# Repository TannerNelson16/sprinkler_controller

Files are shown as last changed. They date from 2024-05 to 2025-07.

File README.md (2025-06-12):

Introduction:
-
Smart irrigation controllers are overpriced and lack customizability so I set out to develop a simple and easy to use solution that is also robust and reliable. The intellidwell sprinkler controller uses custom micropython firmware developed for the ESP32. A localized server that runs right on the microcontroller allows for scheduling, smart phone control, and integration with smart home systems via MQTT. Solid state relays provide extrememely reliable switching of 24VAC solenoid sprinkler valves. A custom 24VAC to 5VDC (variable via a potentiometer) converter allows the logic to be powered from the same source as the sprinkler valve power.

Components used:
-
- ESP32 dev board - https://www.amazon.com/gp/product/B0C7C2HQ7P/ref=ppx_yo_dt_b_search_asin_title?ie=UTF8&psc=1
- Custom PCB - https://github.com/TannerNelson16/sprinkler_controller/blob/master/PCB_files/Sprinkler_Controller_V2/Sprinkler_Controller_V2/Sprinkler_Controller_V2.zip
- PCB parts - https://www.digikey.com/en/mylists/list/P86LUORYGY
- 3d printed container - https://github.com/TannerNelson16/sprinkler_controller/tree/master/V2_Enclosure
- 24v transformer - https://a.co/d/7ivDpOn
- Hardware:
  - https://a.co/d/18vTyet
  - https://a.co/d/1JvqW7l

Web UI:
-
<p float="left">
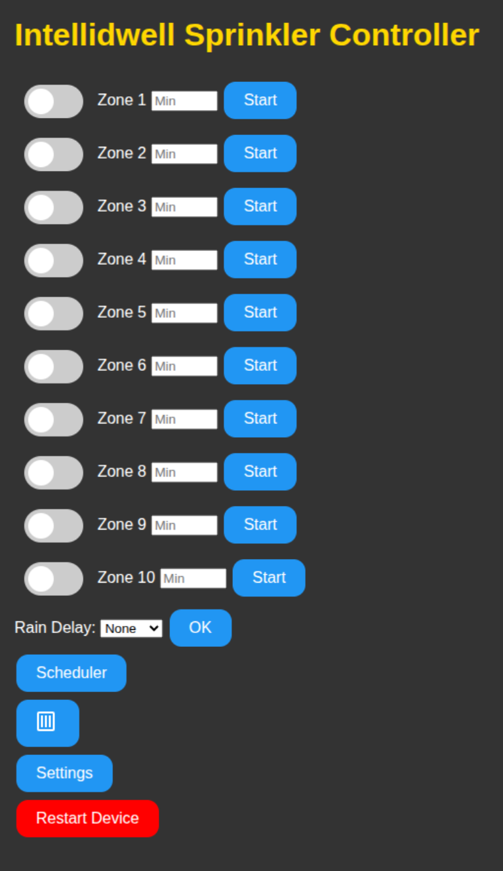
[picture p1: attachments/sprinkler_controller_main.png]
   
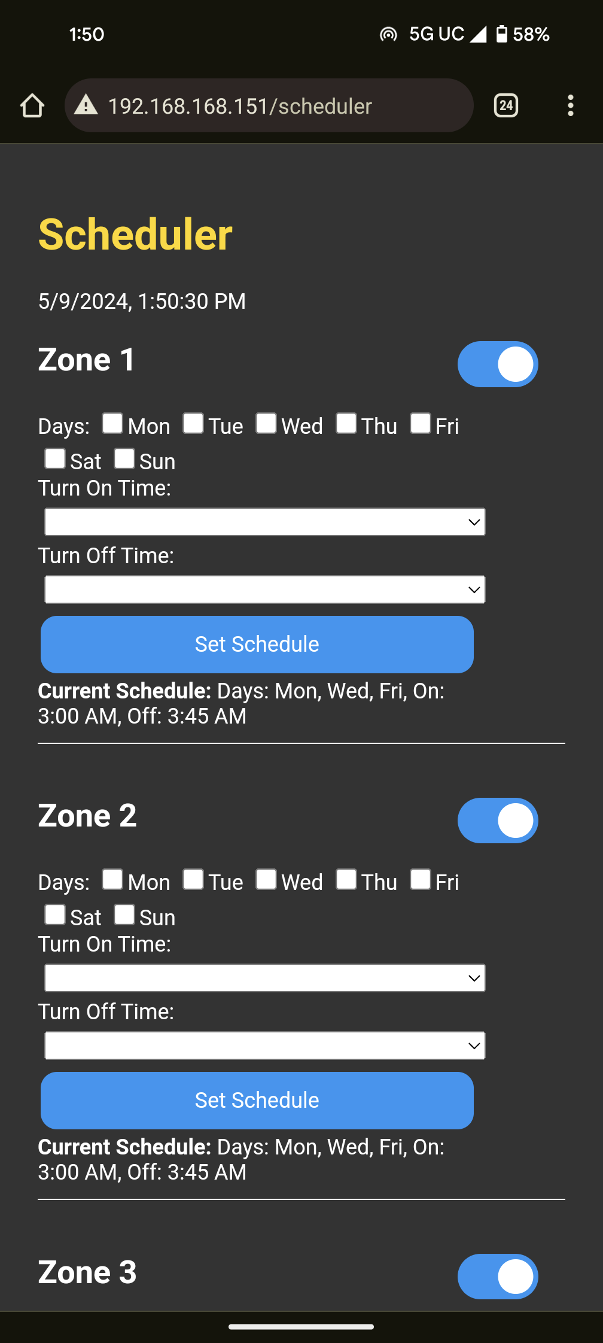
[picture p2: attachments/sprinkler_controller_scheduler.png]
  
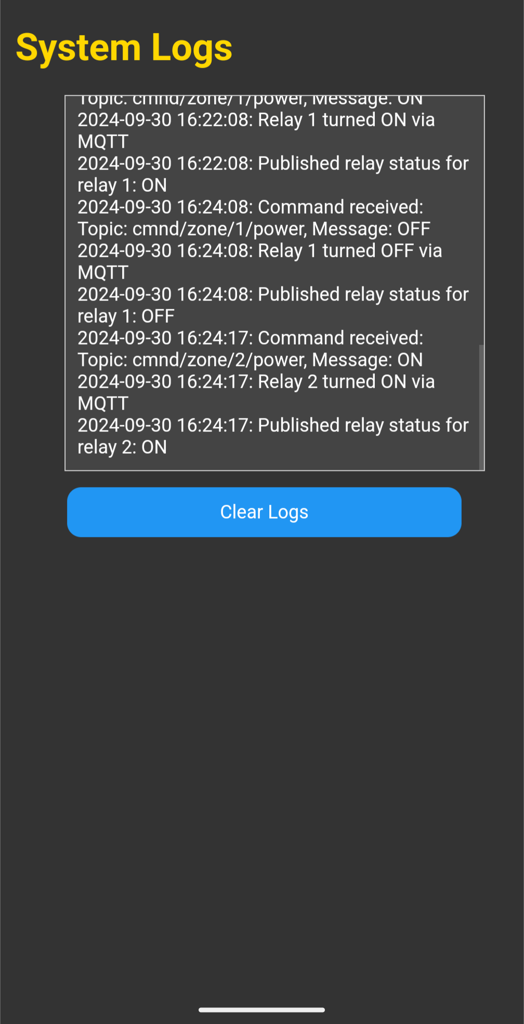
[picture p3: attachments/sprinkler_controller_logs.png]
   
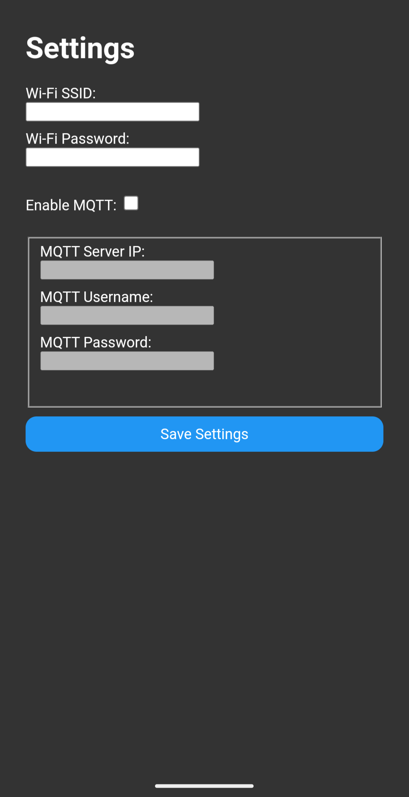
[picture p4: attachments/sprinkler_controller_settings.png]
   

</p>

Installation:
-
FOR LINUX:
--
First install the micropython environment on your ESP32. Here's the official documentation: https://docs.micropython.org/en/latest/esp32/tutorial/intro.html 

For the condensed version:
- Download micropython here: https://micropython.org/resources/firmware/ESP32_GENERIC-20240222-v1.22.2.bin
- Run the following command in the ubuntu terminal:
```
pip install esptool
```
- From the folder where the micropython file is located, run the following commands:
```
esptool.py --chip esp32 --port /dev/ttyUSB0 erase_flash
esptool.py --chip esp32 --port /dev/ttyUSB0 --baud 460800 write_flash -z 0x1000 ESP32_GENERIC-20240222-v1.22.2.bin
```
Once micropython has been successfully installed on the board, download the files in the repository navigate to it's folder.

Once this is complete, save the file and run the following commands:
```
pip install adafruit-ampy
ampy --port /dev/ttyUSB0 put index.html
ampy --port /dev/ttyUSB0 put scheduler.html
ampy --port /dev/ttyUSB0 put logs.html
ampy --port /dev/ttyUSB0 put settings.html
ampy --port /dev/ttyUSB0  put microdot.py
ampy --port /dev/ttyUSB0  put microdot_asyncio.py
ampy --port /dev/ttyUSB0  put controller.py /main.py
```
Reboot and connect to the "intellidwellSC" SSID with password "Sprinkler12345" from any device. In a browser type in 192.168.4.1 to access the sprinkler controller UI.

To connect to a Wifi Network navigate to "Settings" on the main page and enter in your WiFi credentials. You can also input your MQTT credentials here if you wish. When the device is rebooted, you can access the UI from the hostname http://sprinklers.local on your network, the IP address of the device, or from your homeassitant instance via the MQTT integration.

NOTE: If the network is unavailable, the ESP32 will first try to connect without the MQTT integration. If the network is still causing errors, the ESP32 will resume AP mode to allow for control of the sprinkler system. 

Enclosure:
-
<p float="left">
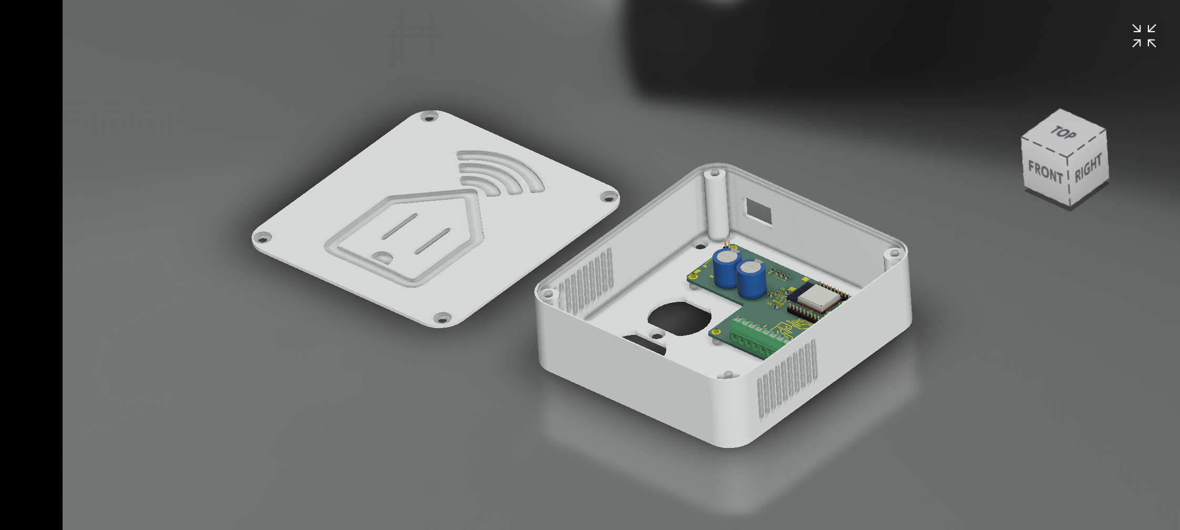
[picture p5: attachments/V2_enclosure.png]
   

Assembly:
-
PCB:
- The PCB has been tested and is fully functional.
- Download the zipped folder here: https://github.com/TannerNelson16/sprinkler_controller/blob/master/PCB_files/Sprinkler_Controller_V2/Sprinkler_Controller_V2/Sprinkler_Controller_V2.zip
- Upload the folder to jlcpcb.com or your chosen pcb manufacturer
- Purchase items from digikey to populate board: https://www.digikey.com/en/mylists/list/P86LUORYGY
- Rocker switches on amazon, if out of stock at digikey: https://a.co/d/f25Jjgr
- Once assembled, and before installing the ESP32, adjust the potentiometer to ensure a 5VDC input to vin and gnd of the ESP32.
<p float="left">
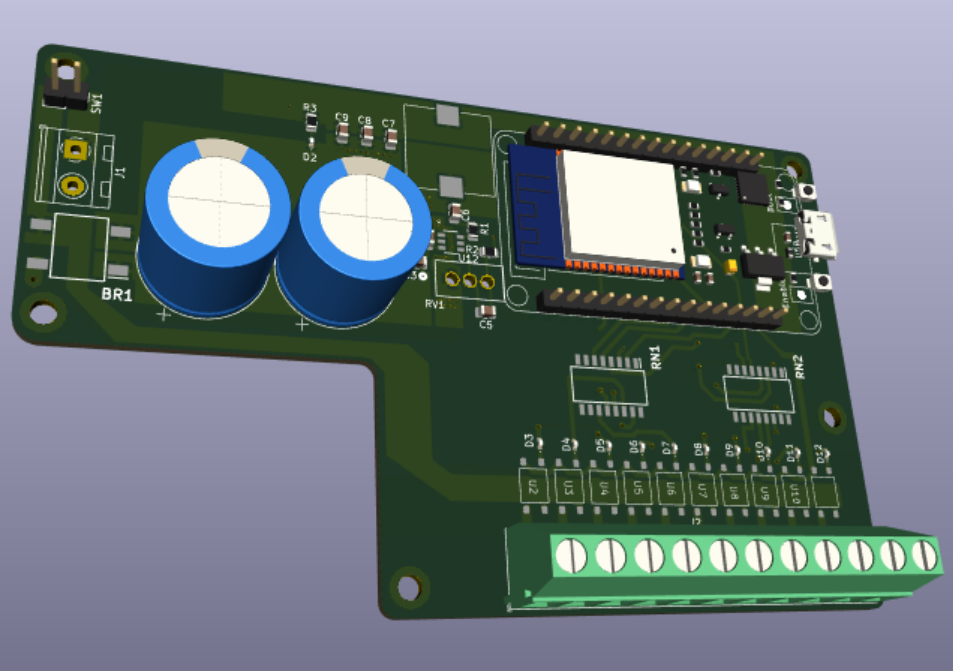
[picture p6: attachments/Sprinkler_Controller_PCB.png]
  
Final Product Images:
-
<p float="left">
   
<p float="left">
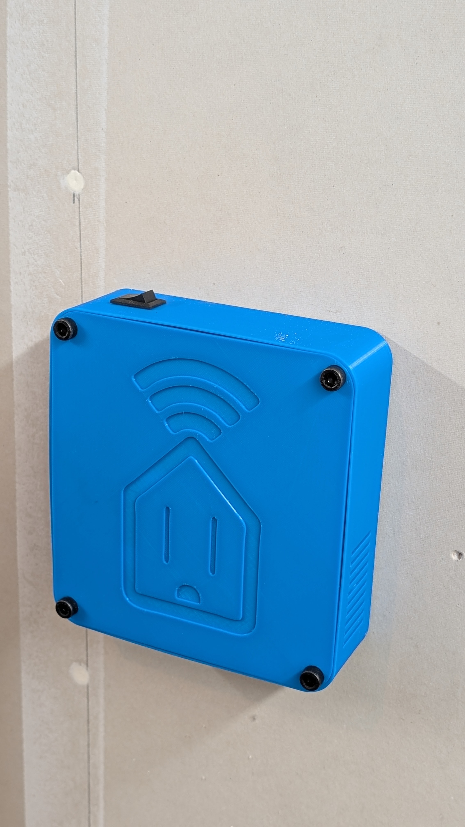
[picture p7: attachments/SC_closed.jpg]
   

Support This Project
-

If you like this project, consider supporting it with a donation!



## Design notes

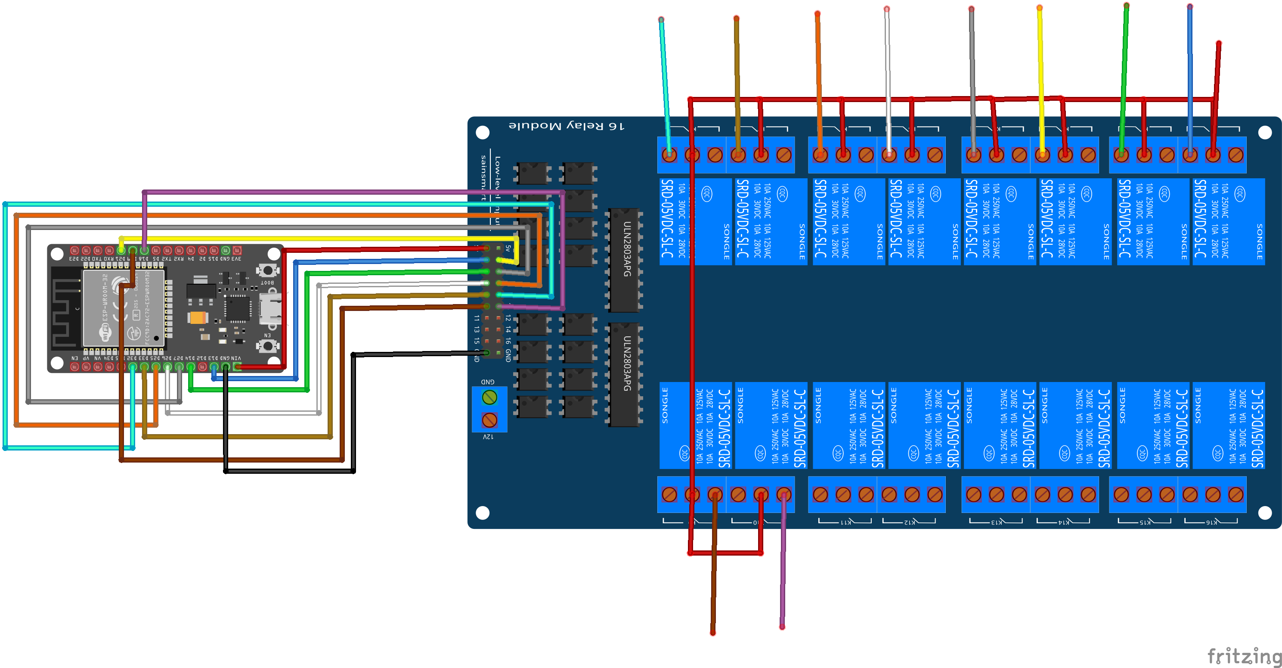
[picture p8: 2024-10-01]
attachments/pinout.png

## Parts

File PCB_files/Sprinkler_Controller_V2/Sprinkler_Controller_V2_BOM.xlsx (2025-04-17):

Country of Origin may be different at time of shipment.
The HTSUS and ECCN information shown is for informational purposes only and is not a representation or warranty as to the accuracy or reliability of these classifications. All information is provided "as is" and is subject to change without notice. Any use made of the information provided is without recourse to Digi-Key and at the user's risk.
Index | Manufacturer Part Number | Manufacturer Name | Description | Availability | Stock Status | Attrition % | Requested Quantity 1 | Pack Quantity 1 | Pack Type 1 | Digi-Key Part Number 1 | Unit Price 1 | Extended Price 1 | Minimum Order Quantity 1 | Customer Reference | Requested Part Number | Lead Weeks | Datasheet | Reference Designator | US Import Tariff | Note | Part Status | RoHS Status | Moisture Sensitivity Level (MSL) | ECCN | HTSUS | Country of Origin | Environmental Information | Original Part numbers | REACH Status | Unit of Measure | Image | Product Notes
1 | B1701URO-20D000114U1930 | Harvatek Corporation | LED RED DIFFUSED 0805 SMD | 9,763 | In Stock |  | 1 | 1 | Cut Tape (CT) | 3147-B1701URO-20D000114U1930CT-ND | 0.10000 | $0.10 | 1 |  | 3147-B1701URO-20D000114U1930TR-ND | 8 | https://mm.digikey.com/Volume0/opasdata/d220001/medias/docus/3739/B1701URO-20D000114U1930.pdf |  | N/A |  | Active | ROHS3 Compliant | 2A (4 Weeks) | EAR99 | 8541.41.0000 | Taiwan | https://mm.digikey.com/Volume0/opasdata/d220001/medias/docus/6223/Harvatek%20Corp%20REACH%20235%20Jun%202023%20Statement.pdf | 3147-B1701URO-20D000114U1930TR-ND | REACH Unaffected | EACH | https://mm.digikey.com/Volume0/opasdata/d220001/medias/images/4847/MFG_3147_B1701.jpg | Non Cancellable Non Returnable.
2 | B1701UYG-20D000114U1930 | Harvatek Corporation | LED YLW-GRN DIFFUSED 0805 SMD | 71,259 | In Stock |  | 10 | 10 | Cut Tape (CT) | 3147-B1701UYG-20D000114U1930CT-ND | 0.09900 | $0.99 | 1 |  | 3147-B1701UYG-20D000114U1930TR-ND | 8 | https://mm.digikey.com/Volume0/opasdata/d220001/medias/docus/3840/B1701UYG-20D000114U1930.pdf |  | N/A |  | Active | ROHS3 Compliant | 2A (4 Weeks) | EAR99 | 8541.41.0000 | Taiwan | https://mm.digikey.com/Volume0/opasdata/d220001/medias/docus/6223/Harvatek%20Corp%20REACH%20235%20Jun%202023%20Statement.pdf | 3147-B1701UYG-20D000114U1930TR-ND | REACH Unaffected | EACH | https://mm.digikey.com/Volume0/opasdata/d220001/medias/images/4847/MFG_3147_B1701.jpg | Non Cancellable Non Returnable.
3 | OR-M406A-TP-G | Shenzhen Orient Components Co., Ltd | SOLID STATE SPST-NO (1 FORM A) S | 2,543 | In Stock |  | 10 | 10 | Cut Tape (CT) | 5007-OR-M406A-TP-GCT-ND | 0.73500 | $7.35 | 1 |  | 5007-OR-M406A-TP-GCT-ND | 8 |  |  | N/A |  | Active | ROHS3 Compliant | 1 (Unlimited) | EAR99 | 8536.41.0030 | China |  | 5007-OR-M406A-TP-GCT-ND | REACH Unaffected | EACH
4 | DF04S | Diodes Incorporated | BRIDGE RECT 1PHASE 400V 1A DF-S | 389 | In Stock |  | 1 | 1 | Tube | DF04SDI-ND | 0.72000 | $0.72 | 1 |  | DF04SDI-ND | 12 | https://www.diodes.com/assets/Datasheets/ds17001.pdf |  | May apply on shipments to the U.S. |  | Active | ROHS3 Compliant | 1 (Unlimited) | EAR99 | 8541.10.0080 | China | https://mm.digikey.com/Volume0/opasdata/d220001/medias/docus/6731/Diode%20RoHS3%20REACH%20247%20Jan%202025%20Statement.pdf | DF04SDI-ND | REACH Unaffected | EACH | https://mm.digikey.com/Volume0/opasdata/d220001/medias/images/5773/31%7EDF-S%7E%7E4.jpg
5 | TB003-500-P02BE | Same Sky (Formerly CUI Devices) | TERMINAL BLOCK, SCREW TYPE, 5.00 | 25,783 | In Stock |  | 1 | 1 | Bag | 102-6161-ND | 0.43000 | $0.43 | 1 |  | 102-6161-ND | 18 | https://www.cuidevices.com/product/resource/tb003-500.pdf |  | May apply on shipments to the U.S. |  | Active | ROHS3 Compliant | Not Applicable | EAR99 | 8536.90.4000 | China | https://www.cuidevices.com/product/resource/material-compliance/tb003-500-series|https://www.cuidevices.com/product/resource/ce-declaration/tb003-500-series | 102-6161-ND | REACH Unaffected | EACH | https://mm.digikey.com/Volume0/opasdata/d220001/medias/images/568/MFG_TB003-500-P02BE.jpg
6 | TB001-500-11BE | Same Sky (Formerly CUI Devices) | TERMINAL BLOCK, SCREW TYPE, 5.00 | 64 | In Stock |  | 1 | 1 | Box | 102-6143-ND | 1.75000 | $1.75 | 1 |  | 102-6143-ND | 18 | https://www.cuidevices.com/product/resource/tb001-500.pdf |  | May apply on shipments to the U.S. |  | Active | ROHS3 Compliant | Not Applicable | EAR99 | 8536.90.4000 | China | https://www.cuidevices.com/product/resource/material-compliance/tb001-500-series|https://www.cuidevices.com/product/resource/ce-declaration/tb001-500-series | 102-6143-ND | REACH Unaffected | EACH | https://mm.digikey.com/Volume0/opasdata/d220001/medias/images/695/MFG_TB001-500-11BE.jpg
7 | 4816P-T01-681LF | Bourns Inc. | RES ARRAY 8 RES 680 OHM 16SOIC | 1,904 | In Stock |  | 2 | 2 | Tube | 4816P-T01-681LF-ND | 2.17000 | $4.34 | 1 |  | 4816P-T01-681LF-ND | 7 | https://www.bourns.com/docs/Product-Datasheets/4800P.pdf |  | N/A |  | Active | ROHS3 Compliant | 1 (Unlimited) | EAR99 | 8533.21.0010 | Costa Rica | https://www.bourns.com/docs/rohs-cofc/41xx_43xx_44xx_48xx_coc.pdf?sfvrsn=376d7ef6_4|https://mm.digikey.com/Volume0/opasdata/d220001/medias/docus/6657/Bourns%20REACH%20247%20Jan%202025%20Statement.pdf | 4816P-T01-681LF-ND | REACH Affected | EACH | https://mm.digikey.com/Volume0/opasdata/d220001/medias/images/6285/118%7E16SOIC-5.59%7E%7E16.jpg
8 | TPP362081-T6TR | 3PEAK | IC REG BUCK ADJ 2A TSOT23-6 | 5,990 | In Stock |  | 1 | 1 | Cut Tape (CT) | 5503-TPP362081-T6TRCT-ND | 0.47000 | $0.47 | 1 |  | 5503-TPP362081-T6TRCT-ND | 9 | https://static.3peak.com/res/doc/ds/Datasheet_TPP36208.pdf |  | May apply on shipments to the U.S. |  | Active | ROHS3 Compliant | 3 (168 Hours) | EAR99 | 8542.39.0060 | China |  | 5503-TPP362081-T6TRCT-ND | REACH Unaffected | EACH | https://mm.digikey.com/Volume0/opasdata/d220001/derivates/6/002/203/016/5503%7ETSOT23-6%7E%7E6_web%28640x640%29.jpg
9 | IFDC5050HZER150M | Vishay Dale | FIXED IND 15UH 7.1A 27 MOHM SMD | 473 | In Stock |  | 1 | 1 | Cut Tape (CT) | 541-IFDC5050HZER150MCT-ND | 0.88000 | $0.88 | 1 |  | 541-IFDC5050HZER150MCT-ND | 14 | https://www.vishay.com/doc?34612 |  | N/A |  | Active | ROHS3 Compliant | 1 (Unlimited) | EAR99 | 8504.50.8000 | Taiwan |  | 541-IFDC5050HZER150MCT-ND | REACH Unaffected | EACH | https://mm.digikey.com/Volume0/opasdata/d220001/medias/images/6128/MFG_IHLP5050FDERxxxxxx_view2.jpg | Non Cancellable Non Returnable.
10 | GRM21BR61H106KE43L | Murata Electronics | CAP CER 10UF 50V X5R 0805 | 158,384 | In Stock |  | 1 | 1 | Cut Tape (CT) | 490-18663-1-ND | 0.28000 | $0.28 | 1 |  | 490-18663-1-ND | 10 | https://search.murata.co.jp/Ceramy/image/img/A01X/G101/ENG/GRM21BR61H106KE43-01A.pdf |  | N/A |  | Active | ROHS3 Compliant | 1 (Unlimited) | EAR99 | 8532.24.0020 | Japan |  | 490-18663-1-ND | REACH Unaffected | EACH | https://mm.digikey.com/Volume0/opasdata/d220001/medias/images/5447/490-Ceramic-Capacitor-Tan-Field.jpg
11 | C2012X5R1V226M125AC | TDK Corporation | CAP CER 22UF 35V X5R 0805 | 137,454 | In Stock |  | 2 | 2 | Cut Tape (CT) | 445-14428-1-ND | 0.58000 | $1.16 | 1 |  | 445-14428-1-ND | 24 | https://product.tdk.com/system/files/dam/doc/product/capacitor/ceramic/mlcc/catalog/mlcc_commercial_general_en.pdf |  | N/A |  | Active | ROHS3 Compliant | 1 (Unlimited) | EAR99 | 8532.24.0020 | Japan | https://product.tdk.com/system/files/dam/doc/product/capacitor/ceramic/mlcc/rohs/mlccrohs_commercial_general_en.pdf|https://product.tdk.com/en/environment/index.html | 445-14428-1-ND | REACH Unaffected | EACH | https://mm.digikey.com/Volume0/opasdata/d220001/medias/images/4846/445_0805-%282012-Metric%29-1%2C45mm-C-Series.jpg
12 | RC0805JR-070RL | YAGEO | RES 0 OHM JUMPER 1/8W 0805 | 269,822 | In Stock |  | 1 | 1 | Cut Tape (CT) | 311-0.0ARCT-ND | 0.10000 | $0.10 | 1 |  | 311-0.0ARCT-ND | 18 | https://www.yageo.com/upload/media/product/products/datasheet/rchip/PYu-RC_Group_51_RoHS_L_12.pdf |  | N/A |  | Active | ROHS3 Compliant | 1 (Unlimited) | EAR99 | 8533.21.0030 | Taiwan | https://www.yageo.com/en/Download/Index/certificates#rchip | 311-0.0ARCT-ND | REACH Unaffected | EACH | https://mm.digikey.com/Volume0/opasdata/d220001/medias/images/4322/cut-tape-render.jpg
13 | CC0805KRX7R9BB104 | YAGEO | CAP CER 0.1UF 50V X7R 0805 | 2,885,384 | In Stock |  | 1 | 1 | Cut Tape (CT) | 311-1140-1-ND | 0.08000 | $0.08 | 1 |  | 311-1140-1-ND | 16 | https://www.yageo.com/upload/media/product/productsearch/datasheet/mlcc/UPY-GPHC_X7R_6.3V-to-250V_24.pdf |  | N/A |  | Active | ROHS3 Compliant | 1 (Unlimited) | EAR99 | 8532.24.0020 | Taiwan |  | 311-1140-1-ND | REACH Unaffected | EACH | https://mm.digikey.com/Volume0/opasdata/d220001/medias/images/4322/cut-tape-render.jpg
14 | RMCF0805FT49R9 | Stackpole Electronics Inc | RES 49.9 OHM 1% 1/8W 0805 | 165,093 | In Stock |  | 1 | 1 | Cut Tape (CT) | RMCF0805FT49R9CT-ND | 0.10000 | $0.10 | 1 |  | RMCF0805FT49R9CT-ND | 17 | https://www.seielect.com/catalog/sei-rmcf_rmcp.pdf |  | N/A |  | Active | ROHS3 Compliant | 1 (Unlimited) | EAR99 | 8533.21.0030 | Taiwan | https://www.seielect.com/catalog/SEI-RoHS_Compliance_Status.pdf|https://www.seielect.com/catalog/reach.pdf|https://www.seielect.com/catalog/sei-coc%20prop%2065.pdf | RMCF0805FT49R9CT-ND | REACH Unaffected | EACH | https://mm.digikey.com/Volume0/opasdata/d220001/medias/images/639/0805-RMCF-Series.jpg
15 | 3296W-1-253LF | Bourns Inc. | TRIMMER 25K OHM 0.5W PC PIN TOP | 988 | In Stock |  | 1 | 1 | Tube | 3296W-253LF-ND | 2.05000 | $2.05 | 1 |  | 3296W-253LF-ND | 10 | https://www.bourns.com/docs/product-datasheets/3296.pdf |  | N/A |  | Active | ROHS3 Compliant | Not Applicable | EAR99 | 8533.40.8050 | Costa Rica | https://www.bourns.com/docs/rohs-cofc/cofc_trim1.pdf?sfvrsn=ec972807_4|https://mm.digikey.com/Volume0/opasdata/d220001/medias/docus/6657/Bourns%20REACH%20247%20Jan%202025%20Statement.pdf | 3296W-253LF-ND | REACH Unaffected | EACH | https://mm.digikey.com/Volume0/opasdata/d220001/medias/images/2383/3296W%20SERIES.jpg
16 | UVK1H102MHD | Nichicon | CAP ALUM 1000UF 20% 50V RADIAL | 532 | In Stock |  | 2 | 2 | Bulk | 493-16111-ND | 1.19000 | $2.38 | 1 |  | 493-16111-ND | 20 | https://www.nichicon.co.jp/english/series_items/catalog_pdf/e-uvk.pdf |  | N/A |  | Active | ROHS3 Compliant | Not Applicable | EAR99 | 8532.22.0020 | Malaysia |  | 493-16111-ND | REACH Affected | EACH | https://mm.digikey.com/Volume0/opasdata/d220001/medias/images/2583/VK%20SERIES%2027mm.JPG
17 | RNCP0805FTD1K00 | Stackpole Electronics Inc | RES 1K OHM 1% 1/4W 0805 | 256,179 | In Stock |  | 1 | 1 | Cut Tape (CT) | RNCP0805FTD1K00CT-ND | 0.10000 | $0.10 | 1 |  | RNCP0805FTD1K00TR-ND | 17 | https://www.seielect.com/catalog/sei-rncp.pdf |  | N/A |  | Active | ROHS3 Compliant | 1 (Unlimited) | EAR99 | 8533.21.0030 | Taiwan | https://www.seielect.com/catalog/SEI-RoHS_Compliance_Status.pdf|https://www.seielect.com/catalog/reach.pdf|https://www.seielect.com/catalog/sei-coc%20prop%2065.pdf | RNCP0805FTD1K00TR-ND | REACH Unaffected | EACH | https://mm.digikey.com/Volume0/opasdata/d220001/medias/images/4322/cut-tape-render.jpg
18 | PPTC151LFBN-RC | Sullins Connector Solutions | CONN HDR 15POS 0.1 TIN PCB | 9,344 | In Stock |  | 2 | 2 | Tray | S7013-ND | 0.89000 | $1.78 | 1 |  | S7013-ND | 11 | https://mm.digikey.com/Volume0/opasdata/d220001/medias/docus/937/Female_Headers.100_DS.pdf |  | N/A |  | Active | ROHS3 Compliant | 1 (Unlimited) | EAR99 | 8536.69.4040 | Taiwan | https://www.sullinscorp.com/wp-content/uploads/2019/03/Sullins-RoHS-Compliant-Statement.pdf|https://www.sullinscorp.com/wp-content/uploads/2021/08/Sullins-REACH-219-SVHC-Compliant-Statement.pdf | S7013-ND | REACH Unaffected | EACH | https://mm.digikey.com/Volume0/opasdata/d220001/medias/images/911/PPTC151LFBN-RC.jpg

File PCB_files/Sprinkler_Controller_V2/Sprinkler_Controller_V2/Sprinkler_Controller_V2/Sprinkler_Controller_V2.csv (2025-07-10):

Id | Designator | Footprint | Quantity | Designation | Supplier and ref
1 | C4 | C_0805_2012Metric | 1 | 10uF
2 | U1 | esp32_devkit_v1 | 1 | ESP32_DevKit_V1_DOIT
3 | C3,C9,C6 | C_0805_2012Metric | 3 | 100nF
4 | D3,D9,D7,D4,D8,D6,D12,D11,D10,D5 | LED_0805_2012Metric_Pad1.15x1.40mm_HandSolder | 10 | LED
5 | U2,U11,U10,U7,U4,U9,U6,U5,U8,U3 | OR-M4XXA | 10 | ~
6 | C5 | C_0805_2012Metric | 1 | C
7 | SW1 | PinHeader_1x02_P2.54mm_Vertical | 1 | SW_SPST
8 | RV1 | RES3_PV36W103C01B00_BRN | 1 | 25k
9 | BR1 | SOP510P1040X260-4N | 1 | DF04S
10 | C8,C7 | C_0805_2012Metric | 2 | 22uF
11 | J2 | TerminalBlock_Phoenix_MKDS-1,5-11_1x11_P5.00mm_Horizontal | 1 | Screw_Terminal_01x11
12 | RN2,RN1 | SOIC127P762X240-16N | 2 | 4816P-T02-681LF
13 | R3 | R_0805_2012Metric | 1 | 1k
14 | L1 | L_Vishay_IHLP-5050 | 1 | 15uH
15 | D2 | LED_0805_2012Metric | 1 | LED
16 | U12 | TSOT23-6-A_TPK | 1 | TPP362081-T6TR
17 | R2 | R_0805_2012Metric | 1 | 49.9
18 | C1,C2 | PCAP_12_5x25-THRU-ELECT_NCA | 2 | 1000uF
19 | R1 | R_0805_2012Metric | 1 | 0
20 | J1 | TerminalBlock_MetzConnect_Type094_RT03502HBLU_1x02_P5.00mm_Horizontal | 1 | Screw_Terminal_01x02

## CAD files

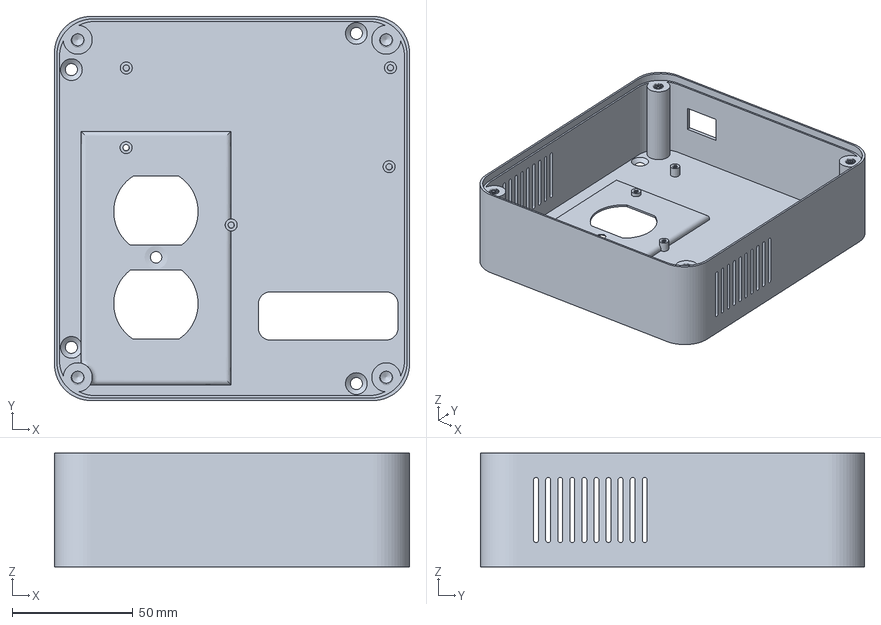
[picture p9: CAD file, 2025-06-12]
V2_Enclosure/SC_enclosure v21_Main.3mf
147.0 x 159.0 x 47.0 mm

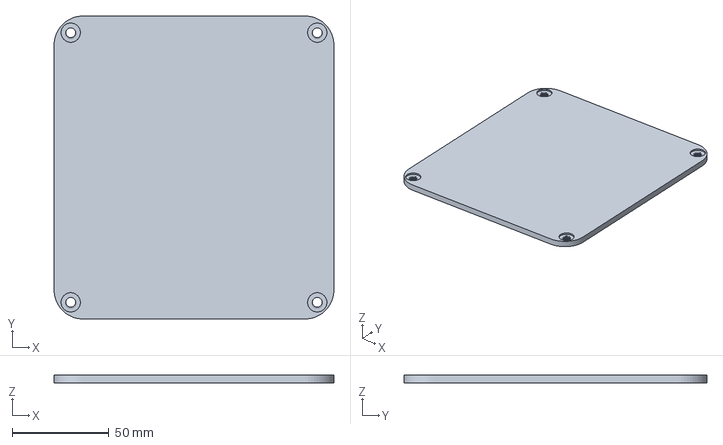
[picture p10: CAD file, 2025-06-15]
V2_Enclosure/SC_enclosure v21_Cover.3mf
145.0 x 157.0 x 4.00 mm

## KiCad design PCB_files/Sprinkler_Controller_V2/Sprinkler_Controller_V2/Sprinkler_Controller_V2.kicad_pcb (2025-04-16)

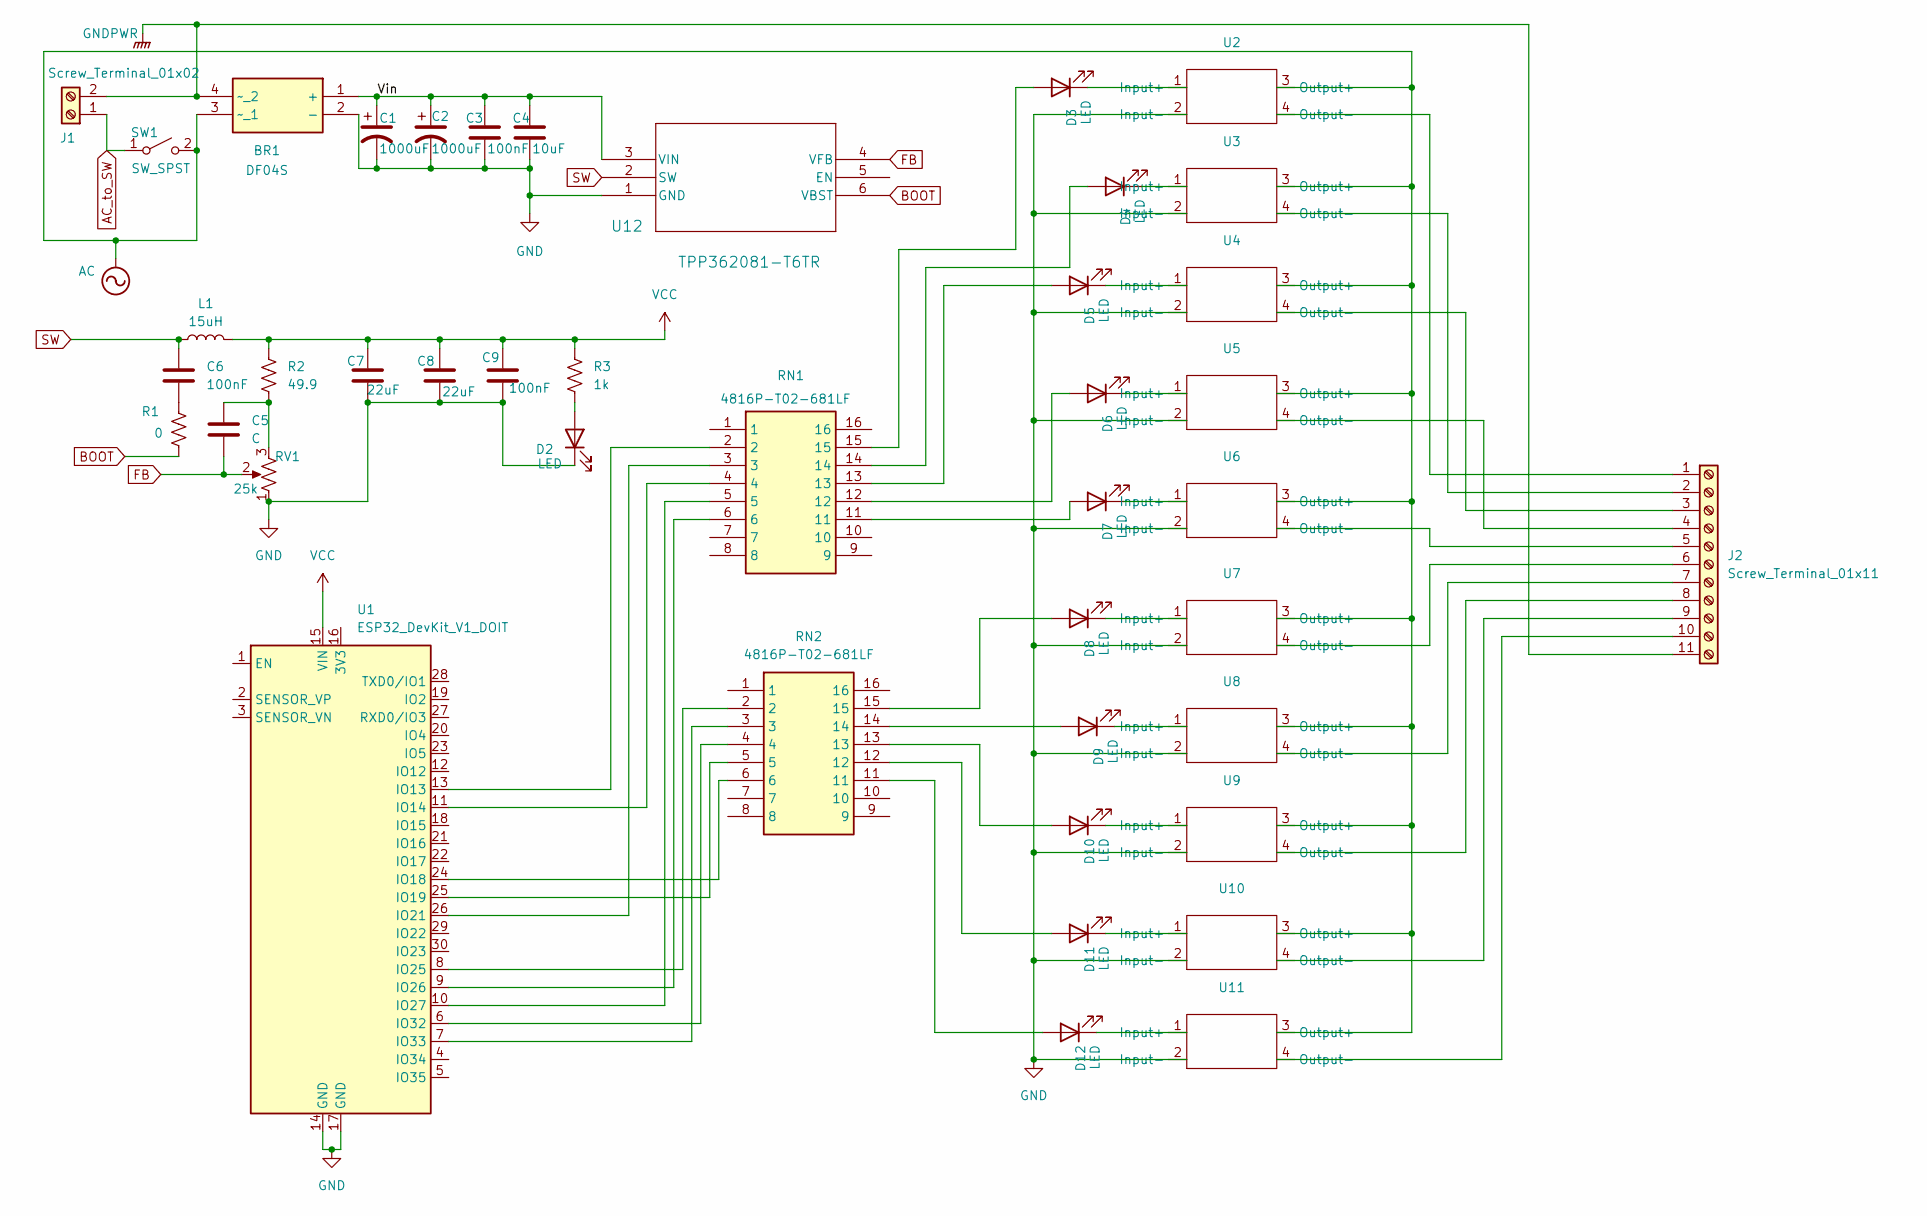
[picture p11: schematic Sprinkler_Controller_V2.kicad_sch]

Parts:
BR1: DF04S; SOP510P1040X260-4N; Manufacturer_Part_Number DF04S
C1, C2: 1000uF; CP_Radial_D16.0mm_P7.50mm
C3, C6, C9: 100nF; C_0805_2012Metric
C4: 10uF; C_0805_2012Metric
C5: C; C_0805_2012Metric
C7, C8: 22uF; C_0805_2012Metric
D2: LED; LED_0805_2012Metric
D3, D4, D5, D6, D7, D8, D9, D10, D11, D12: LED; LED_0805_2012Metric_Pad1.15x1.40mm_HandSolder
J1: Screw_Terminal_01x02; TerminalBlock_MetzConnect_Type094_RT03502HBLU_1x02_P5.00mm_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
J2: Screw_Terminal_01x11; TerminalBlock_Phoenix_MKDS-1,5-11_1x11_P5.00mm_Horizontal
L1: 15uH; L_Vishay_IHLP-5050
R1: 0; R_0805_2012Metric
R2: 49.9; R_0805_2012Metric
R3: 1k; R_0805_2012Metric
RN1, RN2: 4816P-T02-681LF; SOIC127P762X240-16N; Manufacturer_Part_Number 4816P-T02-681LF; Mouser Part Number 652-4816P-T2LF-680
RV1: 25k; RES3_PV36W103C01B00_BRN
SW1: SW_SPST; PinHeader_1x02_P2.54mm_Vertical
U1: ESP32_DevKit_V1_DOIT; esp32_devkit_v1
U2, U3, U4, U5, U6, U7, U8, U9, U10, U11: OR-M4XXA
U12: TPP362081-T6TR; TSOT23-6-A_TPK

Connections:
/Vin: BR1.1 (+), C1.1, C2.1, C3.1, C4.1, U12.3 (VIN)
AC: BR1.3 (~_1), SW1.2 (B), U2.3 (Output+), U3.3 (Output+), U4.3 (Output+), U5.3 (Output+), U6.3 (Output+), U7.3 (Output+), U8.3 (Output+), U9.3 (Output+), U10.3 (Output+), U11.3 (Output+)
AC_to_SW: J1.1, SW1.1 (A)
BOOT: R1.2, U12.6 (VBST)
FB: C5.2, RV1.2, U12.4 (VFB)
GND: BR1.2 (-), C1.2, C2.2, C3.2, C4.2, C7.2, C8.2, C9.2, D2.1 (K), RV1.1, U1.14 (GND), U1.17 (GND), U2.2 (Input-), U3.2 (Input-), U4.2 (Input-), U5.2 (Input-), U6.2 (Input-), U7.2 (Input-), U8.2 (Input-), U9.2 (Input-), U10.2 (Input-), U11.2 (Input-), U12.1 (GND)
GNDPWR: BR1.4 (~_2), J1.2, J2.11
unnamed: C5.1, R2.2, RV1.3
unnamed: C6.2, R1.1
unnamed: D2.2 (A), R3.2
unnamed: D3.2 (A), RN1.15
unnamed: D3.1 (K), U2.1 (Input+)
unnamed: D4.2 (A), RN1.14
unnamed: D4.1 (K), U3.1 (Input+)
unnamed: D5.2 (A), RN1.13
unnamed: D5.1 (K), U4.1 (Input+)
unnamed: D6.2 (A), RN1.12
unnamed: D6.1 (K), U5.1 (Input+)
unnamed: D7.2 (A), RN1.11
unnamed: D7.1 (K), U6.1 (Input+)
unnamed: D8.2 (A), RN2.15
unnamed: D8.1 (K), U7.1 (Input+)
unnamed: D9.2 (A), RN2.14
unnamed: D9.1 (K), U8.1 (Input+)
unnamed: D10.2 (A), RN2.13
unnamed: D10.1 (K), U9.1 (Input+)
unnamed: D11.2 (A), RN2.12
unnamed: D11.1 (K), U10.1 (Input+)
unnamed: D12.2 (A), RN2.11
unnamed: D12.1 (K), U11.1 (Input+)
unnamed: J2.1, U2.4 (Output-)
unnamed: J2.2, U3.4 (Output-)
unnamed: J2.3, U4.4 (Output-)
unnamed: J2.4, U5.4 (Output-)
unnamed: J2.5, U6.4 (Output-)
unnamed: J2.6, U7.4 (Output-)
unnamed: J2.7, U8.4 (Output-)
unnamed: J2.8, U9.4 (Output-)
unnamed: J2.9, U10.4 (Output-)
unnamed: J2.10, U11.4 (Output-)
unnamed: RN1.2, U1.13 (IO13)
unnamed: RN1.4, U1.11 (IO14)
unnamed: RN2.6, U1.24 (IO18)
unnamed: RN2.5, U1.25 (IO19)
unnamed: RN1.3, U1.26 (IO21)
unnamed: RN2.2, U1.8 (IO25)
unnamed: RN1.6, U1.9 (IO26)
unnamed: RN1.5, U1.10 (IO27)
unnamed: RN2.4, U1.6 (IO32)
unnamed: RN2.3, U1.7 (IO33)
SW: C6.1, L1.1, U12.2 (SW)
VCC: C7.1, C8.1, C9.1, L1.2, R2.1, R3.1, U1.15 (VIN)

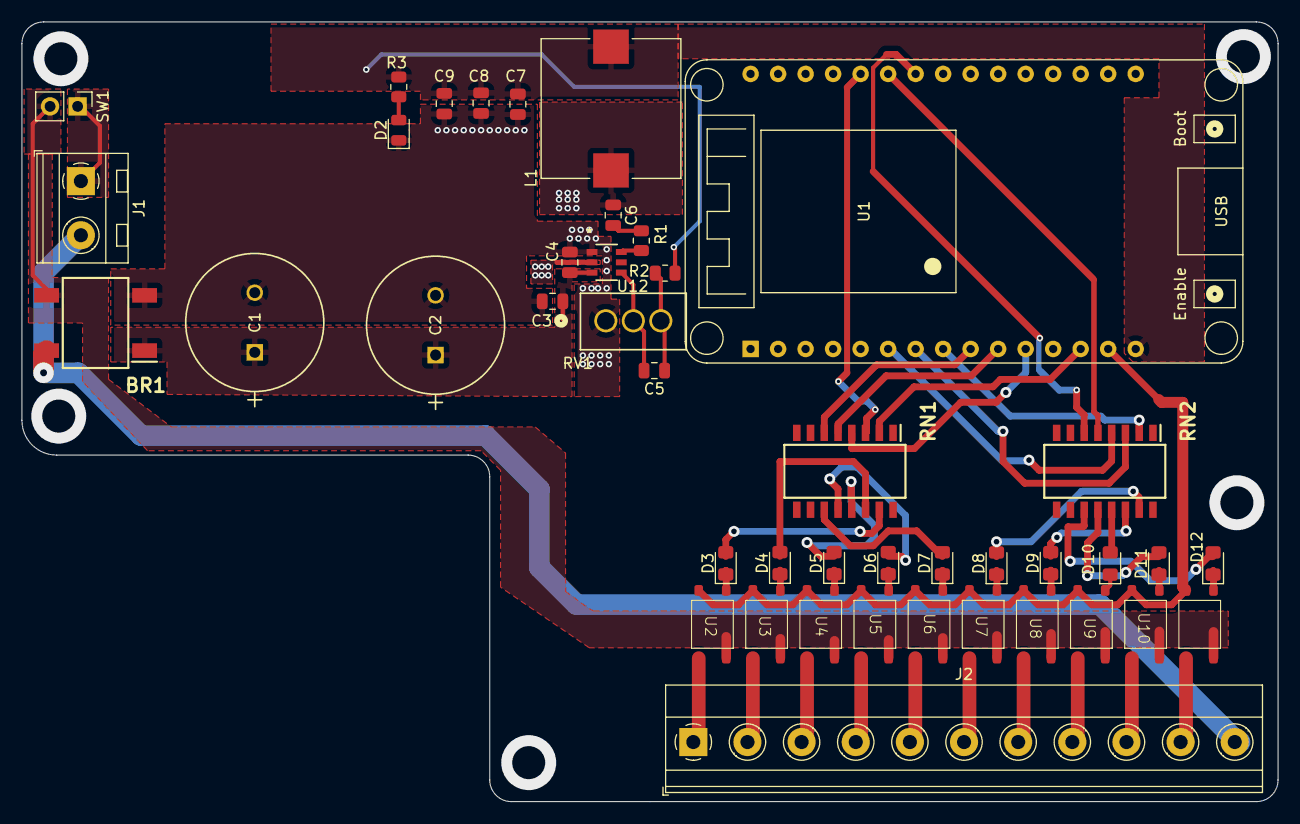
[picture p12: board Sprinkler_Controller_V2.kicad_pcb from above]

Board: 2 copper layers, 116.0 x 72.0 mm, 43 parts (0 on the bottom side), 52 nets.

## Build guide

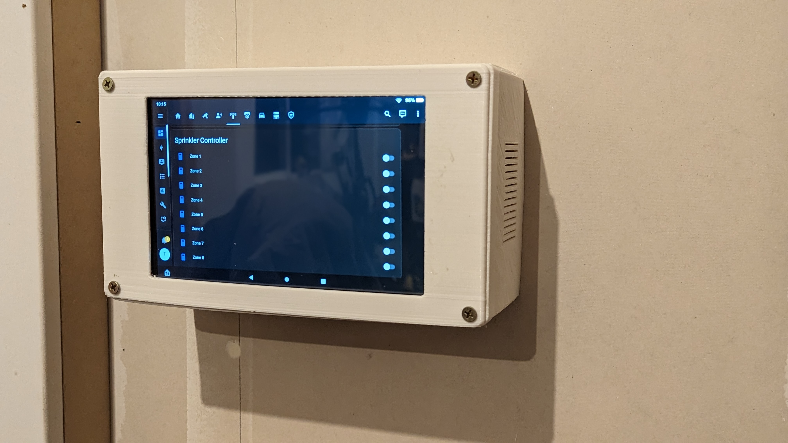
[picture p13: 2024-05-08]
attachments/assembly_2.jpg

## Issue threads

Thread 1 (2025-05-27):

Inverting Outputs

k-archer, 2025-05-27:
I'm setting this up and the relay board I'm using is active low, what would be the easiest way to invert the output pins?

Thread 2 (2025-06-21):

time zone TZ / day light savings DST

clach04, 2025-06-21:
This maybe more of a discussion than an issue.

https://github.com/TannerNelson16/sprinkler_controller/blob/3828a20a5723c7d5c283d38d7fa639a1f48c9e51/controller.py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

Indicates tz is hard coded, a couple of random ideas/suggestions:

1. Mention this in the readme
2. Add a comment in the code that stands out more, for example "EDIT-ME!"
3. Implement timezone name (i.e. database) or rules support

I personally don't think time zone name/database support makes sense on an embedded device due to size requirements when most devices likely remain in a single time zone.

I do think timezone rules make sense, I have an early working micropython implementation that I'm using in my clocks. https://github.com/clach04/py-posix_tz
If you are near Chicago the rule would be something like (not untested):

    CST6CDT,M3.2.0,M11.1.0
Or

    CST6CDT,M3.2.0/2:00:00,M11.1.0/2:00:00

Docs on rules at https://www.gnu.org/software/libc/manual/html_node/TZ-Variable.html

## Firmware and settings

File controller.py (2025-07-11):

from microdot import Microdot, send_file
import network
from machine import Pin, RTC, reset
import machine
import ujson
import json
import time
from time import sleep
from _thread import start_new_thread
import uasyncio as asyncio
from umqtt.simple import MQTTClient
import ntptime
import utime
import uos as os
import gc
import socket
import usocket

machine.sleep(0)       # Disable light sleep
global MQTT

timers = {}


def load_settings():
    try:
        with open('settings.json', 'r') as f:
            config = ujson.load(f)  # Try loading the settings using ujson
            # Ensure the necessary keys exist, if not, provide defaults
            if not isinstance(config, dict):
                raise ValueError("Config is not a valid dictionary.")
            return {
                "ssid": config.get("ssid", ""),
                "wifi_password": config.get("wifi_password", ""),
                "mqtt_server": config.get("mqtt_server", ""),
                "mqtt_username": config.get("mqtt_username", ""),
                "mqtt_password": config.get("mqtt_password", ""),
                "mqtt_enabled": config.get("mqtt_enabled", 0)  # Default to disabled (0) if not present
            }
    except (OSError, ValueError) as e:
        print(f"Error loading settings.json: {e}, loading default settings...")
        return {
            "ssid": "",
            "wifi_password": "",
            "mqtt_server": "",
            "mqtt_username": "",
            "mqtt_password": "",
            "mqtt_enabled": 0  # Default to disabled
        }


    
config = load_settings()


SSID = config['ssid']
PASSWORD = config['wifi_password']
MQTT_BROKER = config['mqtt_server']
MQTT_USER = config['mqtt_username']
MQTT_PASSWORD = config['mqtt_password']
MQTT = config.get('mqtt_enabled', 1) 
# Constants
RELAY_PINS = [13, 21, 14, 27, 26, 25, 33, 32, 19, 18]
relays = [Pin(pin, Pin.OUT) for pin in RELAY_PINS]
wifi = network.WLAN(network.STA_IF)
for relay in relays:
    relay.value(0)


CLIENT_ID = "intellidwell_SC"
TOPIC_BASE = "home/sprinklers/"

client = MQTTClient(CLIENT_ID, MQTT_BROKER, user=MQTT_USER, password=MQTT_PASSWORD, keepalive=0)
client.set_last_will(f"{TOPIC_BASE}status", "Offline", retain=True)

LOG_FILE = 'logs.txt'
LOG_MAX_LINES = 25  # Keep only the last 25 lines of logs
MAX_RECONNECT_ATTEMPTS = 10  # Maximum number of reconnection attempts

#WIFI and MQTT Credentials

def load_settings():
    try:
        with open('settings.json', 'r') as f:
            return json.load(f)
    except OSError:
        # Default settings if file does not exist
        return {
            "ssid": "",
            "wifi_password": "",
            "mqtt_server": "",
            "mqtt_username": "",
            "mqtt_password": ""
        }

def save_settings(settings):
    if settings is None or not isinstance(settings, dict):
        raise ValueError("Invalid settings format. Expected a dictionary.")
    try:
        # Ensure mqtt_enabled is treated as integer 0 or 1
        settings['mqtt_enabled'] = int(settings.get('mqtt_enabled', 0))  
        with open('settings.json', 'w') as f:
            ujson.dump(settings, f)
        log_message("Settings saved successfully.")
    except Exception as e:
        log_message(f"Error saving settings: {e}")




def log_message(message):
    current_time = time.localtime()
    timestamp = "{:04d}-{:02d}-{:02d} {:02d}:{:02d}:{:02d}".format(*current_time[:6])
    log_entry = f"{timestamp}: {message}\n"

    try:
        # Open the log file in append mode and write the log entry
        with open(LOG_FILE, 'a') as f:
            f.write(log_entry)

        # Read the log file, ensuring we keep only the last LOG_MAX_LINES lines
        with open(LOG_FILE, 'r') as f:
            lines = f.read().splitlines()  # Read as a list of strings without the newline characters

        # If the log exceeds the maximum size, write back the trimmed version
        if len(lines) > LOG_MAX_LINES:
            with open(LOG_FILE, 'w') as f:
                f.write("\n".join(lines[-LOG_MAX_LINES:]) + "\n")  # Write lines back as a single string

    except (OSError, AttributeError) as e:
        # Log an error message to the console if writing to the log fails
        print(f"Failed to log message: {e}")
        print(f"LOG ENTRY (Fallback): {log_entry}")

    # Print the log entry to the console for immediate feedback
    print(f"LOG: {timestamp}: {message}")


def command_callback(topic, msg):
    topic = topic.decode()
    msg = msg.decode()
    log_message(f"Command received: Topic: {topic}, Message: {msg}")
    parts = topic.split('/')
    
    if len(parts) == 4 and parts[0] == "cmnd" and parts[1] == "zone" and parts[3] == "power":
        pin = int(parts[2])
        if msg == "ON":
            relays[pin].value(1)
            log_message(f"Relay {pin} turned ON via MQTT")
        elif msg == "OFF":
            relays[pin].value(0)
            log_message(f"Relay {pin} turned OFF via MQTT")
        publish_relay_status(client, pin, relays[pin].value())
    elif len(parts) == 4 and parts[1] == "zone" and parts[3] == "schedule":
        pin = int(parts[2])
        status = msg.lower() == "true"
        if update_schedule_status(pin, status):
            publish_schedule_status(client, pin, status)
        else:
            log_message("Invalid schedule operation")

client.set_callback(command_callback)

async def connect_mqtt():
    try:
        client.connect()
        log_message("MQTT connected.")
        await subscribe_to_topics()
    except Exception as e:
        log_message(f"Failed to connect to MQTT: {e}")
        await asyncio.sleep(5)
        await reconnect()

async def subscribe_to_topics():
    try:
        for i in range(len(relays)):
            client.subscribe(f"cmnd/zone/{i}/power")
            client.subscribe(f"cmnd/zone/{i}/schedule")
            log_message(f"Subscribed to: cmnd/zone/{i}/power and cmnd/zone/{i}/schedule")
        publish_discovery(client)
        publish_schedule_discovery(client)
    except Exception as e:
        log_message(f"Failed to subscribe to topics: {e}")

async def check_messages():
    while True:
        try:
            client.check_msg()
        except OSError as e:
            log_message(f"Failed to check MQTT messages: {e}")
            await reconnect()
        await asyncio.sleep(1)
        gc.collect()  # Run garbage collection to free up memory
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

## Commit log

2024-05-08 added assembly images
2024-05-09 Added required inverse logic for relay board
2024-05-09 added ability to switch schedules on and off
2024-06-27 Fixed bug with mqtt server. added restart button
    [controller.py]
2024-08-05 added pcb files
    [Sprinkler Controller.kicad_pcb, Sprinkler Controller.kicad_sch]
2024-08-06 progress on PCB
    [Sprinkler Controller.kicad_pcb, Sprinkler Controller.kicad_sch]
2024-08-07 board complete
    [Sprinkler Controller-B_Cu.gbr, Sprinkler Controller-B_Mask.gbr, Sprinkler Controller-B_Paste.gbr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]
2024-08-20 fixed memory and logging issues
    [Sprinkler Controller.kicad_pcb, Sprinkler Controller.kicad_sch]
2024-09-23 Started V2 PCB
    [Sprinkler_Controller_V2.kicad_pcb, Sprinkler_Controller_V2.kicad_sch]
2024-09-23 PCB_v2 added pours
    [Sprinkler_Controller_V2.kicad_pcb]
2024-09-24 V2 PCB Complete
    [Sprinkler_Controller_V2-B_Cu.gbr, Sprinkler_Controller_V2-B_Mask.gbr, Sprinkler_Controller_V2-B_Paste.gbr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]
2024-09-30 added web UI connection configuration
    [Sprinkler_Controller_V2.kicad_pcb]
2024-09-30 fixed mqtt push issue
    [controller.py]
2024-10-01 added image of PCB
2024-10-17 changed switch polarity for new PCB design
2024-10-17 changed C1,C2 capacitor values
    [Sprinkler_Controller_V2.kicad_pcb, Sprinkler_Controller_V2.kicad_sch]
2024-10-17 updated gerbers
    [Sprinkler_Controller_V2-B_Cu.gbr, Sprinkler_Controller_V2-B_Mask.gbr, Sprinkler_Controller_V2-B_Paste.gbr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]
2024-10-17 added mDNS
    [Sprinkler_Controller_V2.kicad_pcb]
2024-10-21 added enclosure for new pcb design
    [Sprinkler_Controller_V2_Cover.stl, Sprinkler_Controller_V2_Main_Box.stl]
2024-10-24 fixed zones turning off on wrong days, changed time sync to once per day
    [controller.py]
2025-03-15 updated size of leds on pcb
    [Sprinkler_Controller_V2.csv, Sprinkler_Controller_V2.kicad_pcb, Sprinkler_Controller_V2.kicad_sch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]
2025-04-09 cleaned up schematic
    [Sprinkler_Controller_V2.kicad_sch]
2025-04-14 cleaned schematic
2025-04-16 Changed capacitors
    [Sprinkler_Controller_V2.kicad_pcb]
2025-04-17 updated gerber file
    [Sprinkler_Controller_V2-B_Cu.gbr, Sprinkler_Controller_V2-B_Mask.gbr, Sprinkler_Controller_V2-B_Paste.gbr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]
2025-04-17 cleaned up files
    [Sprinkler Controller-B_Cu.gbr, Sprinkler Controller-B_Mask.gbr, Sprinkler Controller-B_Paste.gbr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]
2025-06-12 updated enclosure
    [SC_enclosure v21_Cover.3mf, SC_enclosure v21_Main.3mf, Sprinkler_Controller_V2_Cover.stl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]
2025-06-15 updated 3mf files
    [SC_enclosure v21_Cover.3mf]
2025-06-15 3mf cover fix
    [SC_enclosure v21_Cover.3mf]
2025-06-21 added timer to each zone, and a rain delay function
2025-07-10 fixed typos, removed extra logging, modified mobile UI buttons
    [Sprinkler_Controller_V2.csv]
